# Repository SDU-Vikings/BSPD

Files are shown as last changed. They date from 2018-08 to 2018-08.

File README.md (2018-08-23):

# BSPD
Formula Student -- Brake System Plausibility Device

# Brake System Plausibility Device 

Formula Student  
Ruleset: FS-Rules_2018_V1.1  
This BSPD passed scrutineering at Formula Student UK 2018  
Please let us know if you used this design for your car or if you have used it and made useful improvements to it  
Also if you have any questions please let us know --> [SDU-Vikings](https://www.facebook.com/SDUVikings/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)

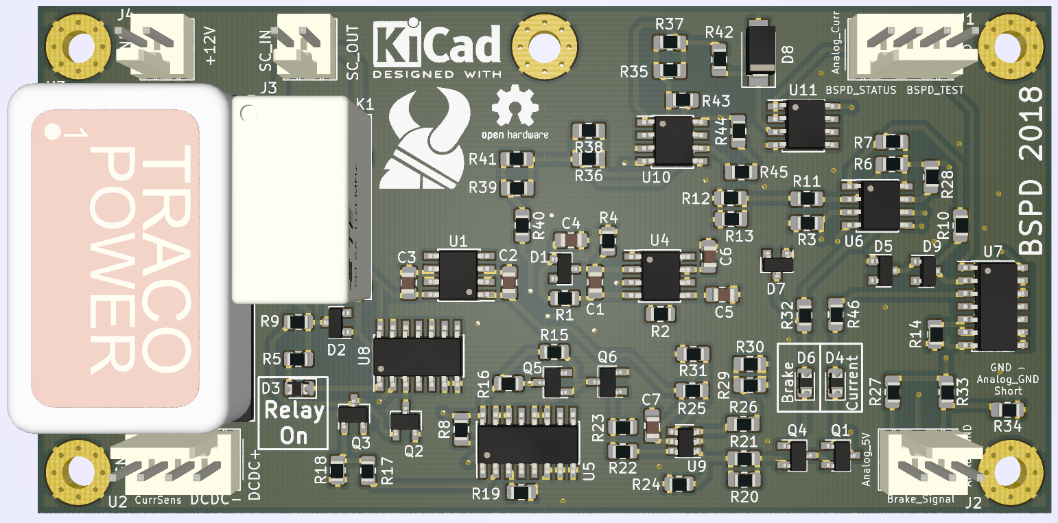
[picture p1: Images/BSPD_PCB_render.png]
BSPD PCB Render


## Schematic and PCB

The project is made in KiCad. Get it here --> [KiCad 5.0](http://kicad-pcb.org/download/)  
The schematic layout and PCB layout is found in the ``KiCad/`` subfolder.

## Components

The design is made for a battery supply of between 11 V and 15 V.   
The current consumption is measured at between 63,0 and 90,3 mA with a 12,7 V supply.

For current measurement [LEM HAS 100-S](https://export.rsdelivers.com/product/lem/has-100s/lem-has-series-open-loop-current-sensor-300a/3019495) is used. The Hall Effect Sensor needs +-15 V supply hence the [TEN 8-1223](https://export.rsdelivers.com/product/tracopower/ten-8-1223/tracopower-ten-8-8w-isolated-dc-dc-converter/4239628).  
For brake presssure measurement [EPT3100](https://www.variohm.com/images/datasheets/EPT3100_Pressure_Sensor_1608_T.pdf) is used.  
The relay for the safety chain is [TE-OJ-SS-112LMH2](https://export.rsdelivers.com/product/te-connectivity/oj-ss-112lmh2005/te-connectivity-spno-non-latching-relay-pcb-mount/6802518).

### Debugging LED's

The design includes SMD-sized LED's for easier debugging. **D3** and **D4** can be removed altogether and **D6** replaced by an ordinary P/N-diode.

### Delay-block

[LTC6994](https://export.rsdelivers.com/product/linear-technology/ltc6994is6-1trmpbf/linear-technology-ltc6994is6-1trmpbf-programmable/8580894) is as delay-block. The delay-block is configured for a delay of 500 ms. See [LTC6994 One Shot](http://beta-tools.analog.com/timerblox/LTC6994) to configure delay and use ``LTC6994.json`` for the setup.

### Latch and latch-reset

The signal from the delay-block is received by a latch [CD4043B](https://export.rsdelivers.com/product/texas-instruments/cd4043bd/texas-instruments-cd4043bd-quad-latch-transparent/6607616) that will latch on to the signal requiring power cycling of the low voltage system to reset it again.  
However the latch will latch on to a high signal when the low voltage system is turned on initially. The 555-circuit is used for generating a pulse, that will reset the latch. The pulse has a delay of approximately 500 ms at turn on. 

## Input signals and voltage dividers

### Current

HAS_100-S has a output voltage range of -12V to +12V with a voltage signal of 4 V for every 100 A in the wire.   
With a nominal battery voltage of 510,6 V the current to the motors at 9,8 A is below 5 kW as required by EV7.5.5 in the rules.  
```math
510,6 \,\mathrm{V} \cdot 9,7 \,\mathrm{A} \approx 4.953 \,\mathrm{W} 
```

At this current in the HV-wires the voltage output from the hall effect sensor is 0,388 V.  
The voltage divider between **R6** and **R11+R12||R13** gives a voltage treshold of 0,380, which corresponds to a current of 9,5 A in the wires.

```math
\frac{2600}{100000 + 2600} \cdot 15\, \mathrm{V} \approx 0,380\, \mathrm{V}
```

Change the value of **R6**, **R11**, **R12** and **R13** to adjust the voltage treshold of the comparator.

### Brake

Change the value of **R27** and **R33** to adjust the voltage treshold of the comparator for the brake pressure sensor.

## Current Measurement

The design includes operational amplifiers whose purpose is to convert the voltage range of the hall effect sensor signal from (-12V/+12V) to (0V/10V) for interfacing with a controller.  
It is not required for the intended functionality of the BSPD and can be removed.

**U10B** is a summation operational amplifier. The gain on the current sensor output is -5/24. This is summed to a voltage of -2,5 V converting the voltage range to (-5 V/0V). **U10A** has a gain of -2 converting the voltage range to the desired (0V/10V). **U11A** is a buffer.

## Labels in the schematic

``DCDC+``           +15 V  
``DCDC-``           -15 V  
``BSPD_TEST``       - Signal from controller to simulate 5 kW drawn from the battery pack  
``BSPD_STATUS``     - Signal to controller to show BSPD status. High when there is a BSPD fault  
``SC_IN``           - Safety chain in  
``SC_OUT``          - Safety chain out  
``Latch_Reset``     - From 555-timer-circuit. Used to pulse reset the latch   
``Current_Sensor``  - Voltage signal from LEM HAS 100-S  
``Brake_Sensor``    - Voltage signal from EPT3100  
``Analog_GND``      - Supplied GND to EPT3100. This is shorted to GND at the controller  
``Analog_5V``       - 5 V supplied to EPT3100

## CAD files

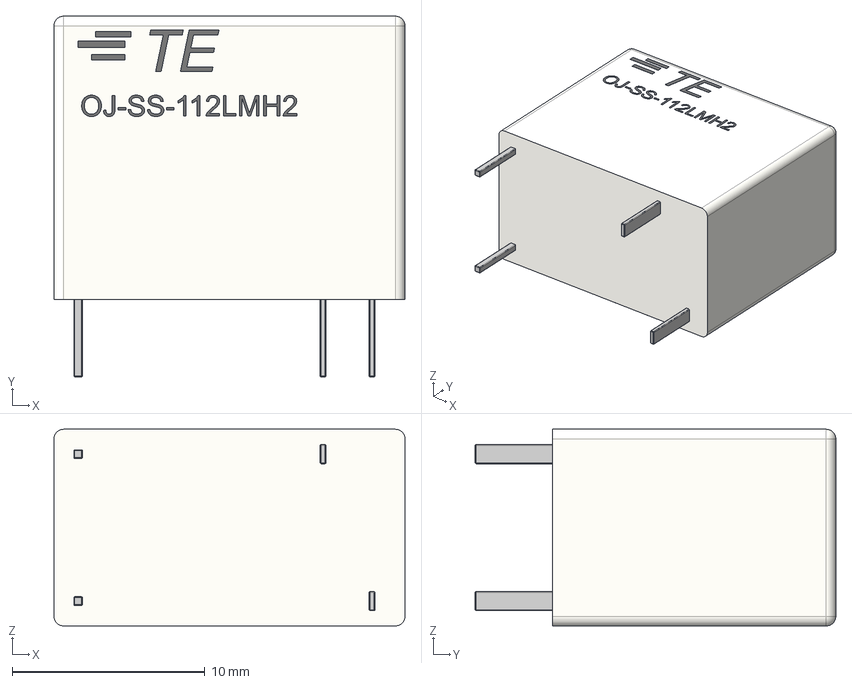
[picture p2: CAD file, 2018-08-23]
KiCad/TE-OJ-SS-112LMH2 v2.step
18.2 x 18.7 x 10.2 mm

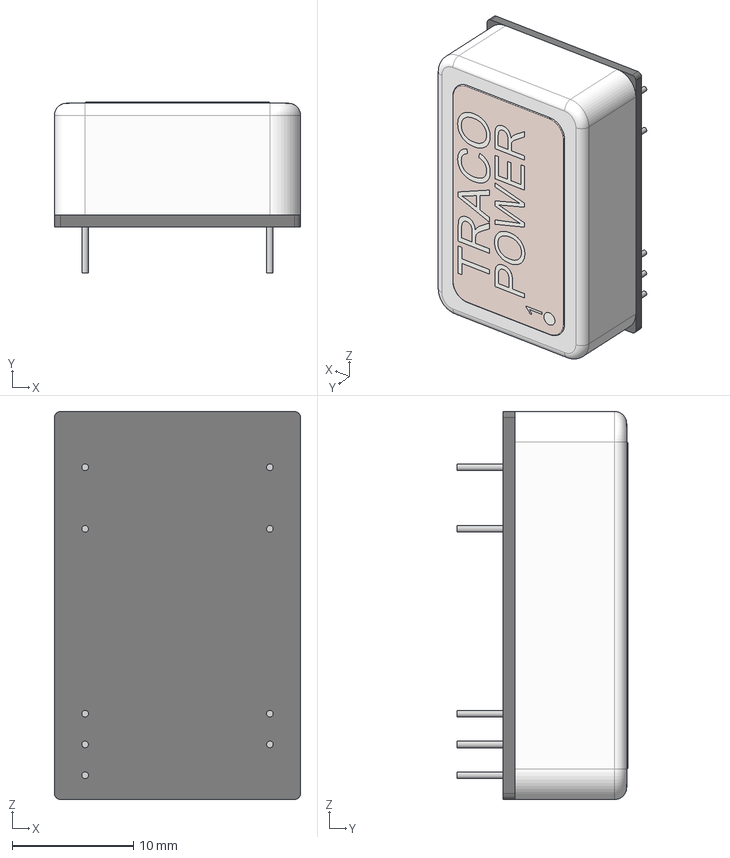
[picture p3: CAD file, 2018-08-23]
KiCad/TEN 8-1223 v4.step
20.3 x 14.1 x 32.0 mm

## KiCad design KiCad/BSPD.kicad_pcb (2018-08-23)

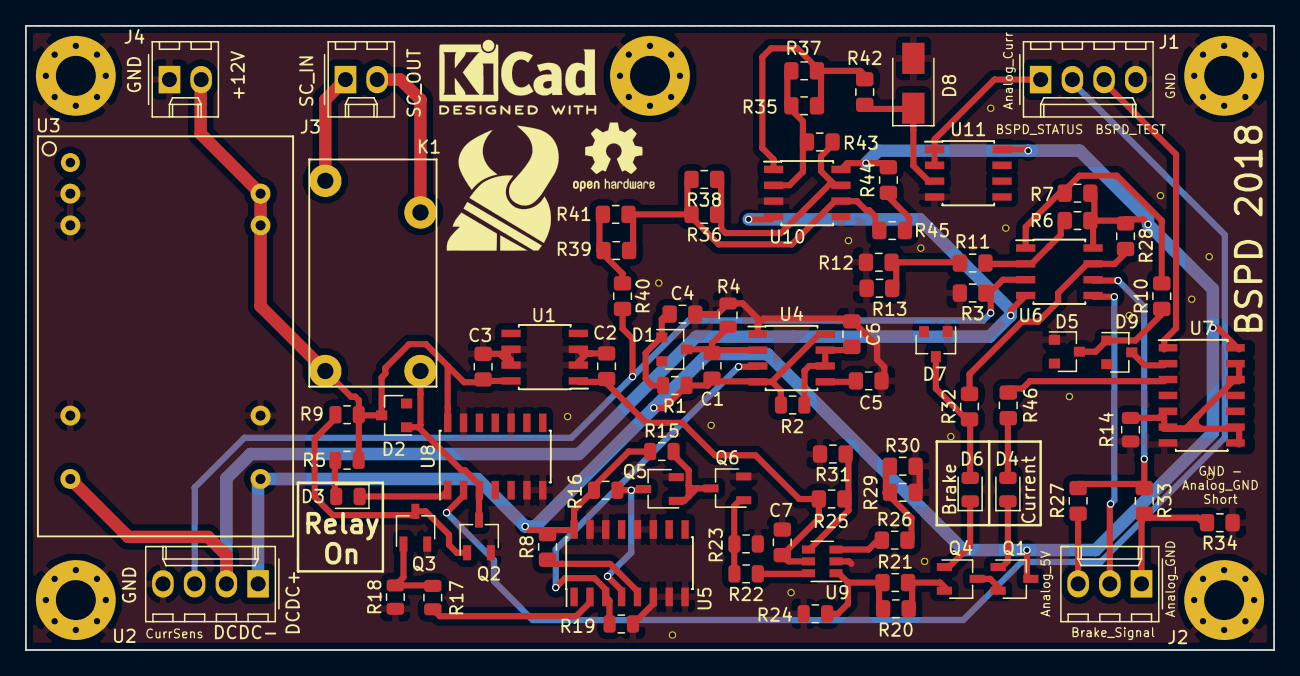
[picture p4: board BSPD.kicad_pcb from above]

Board: 2 copper layers, 100.0 x 50.0 mm, 84 parts (0 on the bottom side), 56 nets.

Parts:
C1: 1µ; C_0805_2012Metric_Pad1.15x1.40mm_HandSolder
C2, C7: 0,1 µF; C_0805_2012Metric_Pad1.15x1.40mm_HandSolder
C3: 0,33 µF; C_0805_2012Metric_Pad1.15x1.40mm_HandSolder
C4, C6: 4,7µ; C_0805_2012Metric_Pad1.15x1.40mm_HandSolder
C5: 100n; C_0805_2012Metric_Pad1.15x1.40mm_HandSolder
D1, D2, D5, D7, D9: BAS16LT1; D_SOT-23_ANK
D3, D4, D6: LED; D_0805_2012Metric
D8: 10V; D_SMA
J1: Conn_01x04; Molex_KK-254_AE-6410-04A_1x04_P2.54mm_Vertical
J2: Conn_01x03; Molex_KK-254_AE-6410-03A_1x03_P2.54mm_Vertical
J3, J4: Conn_01x02; Molex_KK-254_AE-6410-02A_1x02_P2.54mm_Vertical
K1: TE-OJ-SS-112LMH2; TE-OJ-Series_Miniature-PCB-Relay
Q1, Q4: MMBT3904; TSOT-23
Q2, Q3, Q5, Q6: 2N7002; TSOT-23
R1, R2, R4, R5, R9, R14, R15, R16, R18, R19, R23: 10k; R_0805_2012Metric
R3, R6: 100k; R_0805_2012Metric_Pad1.15x1.40mm_HandSolder
R7, R8, R10, R27, R28, R32, R33, R36, R38, R42, R43, R46: 10k; R_0805_2012Metric_Pad1.15x1.40mm_HandSolder
R11, R13, R41: 2,2k; R_0805_2012Metric_Pad1.15x1.40mm_HandSolder
R12: 220; R_0805_2012Metric_Pad1.15x1.40mm_HandSolder
R17, R22: 33; R_0805_2012Metric
R20, R21: 3,3k; R_0805_2012Metric_Pad1.15x1.40mm_HandSolder
R24: 680; R_0805_2012Metric
R25: 1M; R_0805_2012Metric_Pad1.15x1.40mm_HandSolder
R26: 68k; R_0805_2012Metric_Pad1.15x1.40mm_HandSolder
R29: 33k; R_0805_2012Metric_Pad1.15x1.40mm_HandSolder
R30: 150k; R_0805_2012Metric_Pad1.15x1.40mm_HandSolder
R31: 680k; R_0805_2012Metric_Pad1.15x1.40mm_HandSolder
R34: 0; R_0805_2012Metric_Pad1.15x1.40mm_HandSolder
R35: 220k; R_0805_2012Metric_Pad1.15x1.40mm_HandSolder
R37, R39, R40: 22k; R_0805_2012Metric_Pad1.15x1.40mm_HandSolder
R44, R45: 15k; R_0805_2012Metric_Pad1.15x1.40mm_HandSolder
U1: L78L05_SO8; SOIC-8_3.9x4.9mm_P1.27mm
U2: HAS_100-S; Molex_KK-254_AE-6410-04A_1x04_P2.54mm_Vertical
U3: TEN8-1223
U4: LM555; SOIC-8_3.9x4.9mm_P1.27mm
U5: CD4043B; SOIC-16_3.9x9.9mm_P1.27mm
U6: LM2903; SOIC-8_3.9x4.9mm_P1.27mm
U7: HEF4071; SOIC-14_3.9x8.7mm_P1.27mm
U8: CD4041UB; SOIC-14_3.9x8.7mm_P1.27mm
U9: LTC6994; SOT-23-6
U10, U11: TL072; SOIC-8_3.9x4.9mm_P1.27mm

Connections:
+5V: C2.1, C7.1, R25.1, U1.1, U9.5
+12V: C3.1, D2.1, J4.2, K1.1, R5.1, R9.1, U1.8, U3.22, U3.23, U8.14
/Sheet5B6518BB/Analog_HV_Current_Measurement: J1.1, U11.1, U11.2
Analog_5v: J2.3, R27.1
Analog_GND: J2.1, R33.2, R34.2
BSPD_STATUS: J1.2, U8.2
BSPD_TEST: J1.3, U7.1
Brake_Signal: J2.2, U6.5
Current_Sensor_Out: R3.1, R40.2, U2.3, U6.3
DCDC+: C1.1, Q1.3, R1.1, R2.1, R6.1, R7.1, R8.2, R15.1, R16.1, R28.1, R44.2, U2.1, U3.14, U4.4, U4.8, U5.16, U6.8, U7.14, U10.8, U11.8
DCDC-: U2.2, U3.11, U6.4, U10.4
GND: C2.2, C3.2, C4.2, C5.2, C6.2, C7.2, D5.2, D7.2, D8.2, J1.4, J4.1, Q2.2, Q3.2, Q5.2, Q6.2, R3.2, R4.2, R12.2, R13.2, R14.2, R18.1, R19.1, R23.1, R24.1, R29.2, R30.2, R31.2, R34.1, U1.2, U1.3, U1.6, U1.7, U2.4, U3.2, U3.3, U3.9, U3.16, U4.1, U5.6, U5.7, U5.8, U5.11, U5.12, U5.14, U5.15, U7.7, U8.6, U8.7, U8.10, U8.13, U9.2, U10.3, U10.5, U11.4
Latch_Reset: R19.2, U4.3, U5.3
unnamed: C1.2, D1.1, R4.1, U4.2
unnamed: C4.1, D1.2, R1.2
unnamed: C5.1, U4.5
unnamed: C6.1, R2.2, U4.6, U4.7
unnamed: D2.2, K1.2, Q2.3, U8.3
unnamed: D3.1, U8.1
unnamed: D3.2, R5.2
unnamed: D4.1, Q1.1
unnamed: D4.2, R46.1
unnamed: D5.1, D9.2, R10.1
unnamed: D6.1, Q4.1
unnamed: D6.2, D7.1, R32.1
unnamed: D8.1, R42.2, U11.3
unnamed: D9.1, U7.2
unnamed: Q1.2, Q4.3
unnamed: Q2.1, Q3.3, R9.2
unnamed: Q3.1, R17.2, R18.2
unnamed: Q4.2, R20.2, R21.2
unnamed: Q5.1, Q6.3, R15.2
unnamed: Q5.3, R16.2, U5.4
unnamed: Q6.1, R22.2, R23.2
unnamed: R8.1, U5.5
unnamed: R7.2, R10.2, U6.1
unnamed: R6.2, R11.1, U6.2
unnamed: R11.2, R12.1, R13.1
unnamed: R14.1, U7.5, U7.6, U7.8, U7.9, U7.12, U7.13
unnamed: R17.1, U5.2
unnamed: R20.1, R21.1, R24.2, U9.1
unnamed: R22.1, U9.6
unnamed: R25.2, R31.1, U9.4
unnamed: R26.1, U9.3
unnamed: R26.2, R29.1, R30.1
unnamed: R27.2, R33.1, U6.6
unnamed: R28.2, R32.2, U6.7
unnamed: R35.1, R37.1, R42.1, U10.1
unnamed: R35.2, R37.2, R43.1, U10.2
unnamed: R36.1, R38.1, R43.2, U10.7
unnamed: R36.2, R38.2, R39.1, R41.1, R45.1, U10.6
unnamed: R39.2, R40.1, R41.2
unnamed: R44.1, R45.2
unnamed: R46.2, U7.3
SC_IN: J3.1, K1.4
SC_OUT: J3.2, K1.3
